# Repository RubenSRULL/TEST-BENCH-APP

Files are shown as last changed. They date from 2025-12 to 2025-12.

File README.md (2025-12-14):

# Banco de Pruebas para Motores Eléctricos con ESP32

## Descripción general

Este proyecto implementa un **banco de pruebas automatizado para motores eléctricos con hélice**, permitiendo la medición y visualización en tiempo real de **velocidad de rotación (RPM), empuje, par y consumo de corriente**.

El sistema está compuesto por:
- Un **microcontrolador ESP32** encargado del control del motor y la adquisición de sensores.
- Un **broker MQTT** para la comunicación.
- Una **aplicación web desarrollada con Dash (Python)** que actúa como interfaz de usuario (HMI).

---

## Arquitectura del sistema

Arquitectura cliente-servidor basada en MQTT:

- ESP32 → Publica datos de sensores
- Dash App → Envía comandos y visualiza resultados
- Mosquitto → Broker MQTT intermedio

---

## Características principales

- Control de velocidad del motor por PWM  
- Ensayo automático por pasos configurables  
- Medición de:
  - RPM
  - Empuje (celda de carga)
  - Par (celda de carga)
  - Corriente eléctrica
- Visualización gráfica en tiempo real  
- Interfaz web intuitiva  
- Comunicación inalámbrica vía WiFi + MQTT  
- Sistema basado en máquina de estados  

---

## Hardware utilizado

- ESP32  
- Módulo HX711 (x2)  
- Celdas de carga (x2)  
- Sensor de corriente ACS712 (30 A)
- Tacómetro  
- Controlador ESC  
- Motor brushless + hélice  
- Fuente de alimentación +12 V

---

## Software utilizado

### ESP32
- Arduino IDE
- Librerías:
  - `HX711`
  - `WiFi`
  - `ArduinoJson`
  - `PubSubClient`

### Aplicación de usuario
- Python 3.10+
- Librerías:
  - `dash`
  - `plotly`
  - `paho-mqtt`

### Comunicación
- Mosquitto MQTT Broker

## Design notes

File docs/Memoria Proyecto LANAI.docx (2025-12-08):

Máster en Informática Industrial y Robótica

Banco de pruebas para la caracterización de sistema de propulsión motor - hélice

Test bench for the characterization of the engine-propeller propulsion system

Autor

La Laguna, 8 de diciembre de 2025

Memoria Proyecto Final

Licencia

© Esta obra está bajo una licencia de Creative Commons Reconocimiento 4.0 Internacional.

Resumen

El objetivo de este trabajo ha sido el diseño y construcción de un banco de pruebas destinado a la caracterización de sistemas de propulsión motor–hélice. Para ello se integró un microcontrolador ESP32 encargado de la adquisición de datos y del control del motor BLDC, así como un sistema de comunicación MQTT que permite la transmisión de información en tiempo real hacia un dispositivo remoto.

Además, se implementó una aplicación web desarrollada en Python, mediante la cual el usuario puede supervisar el funcionamiento del sistema, enviar órdenes de control y visualizar las variables medidas durante cada ensayo.

Este banco de pruebas pretende constituir una plataforma de bajo costo, adecuada para el análisis de distintos conjuntos motor–hélice utilizados en drones.

Palabras clave: Drones, Banco de pruebas, motor BLDC, hélice, MQTT, ESP32, C, Python

Abstract

The objective of this work has been the design and construction of a test bench intended for the characterization of motor–propeller propulsion systems. For this purpose, an ESP32 microcontroller was integrated to handle data acquisition and control of the BLDC motor, as well as an MQTT communication system that enables real-time data transmission to a remote device.

In addition, a web application developed in Python was implemented, allowing the user to monitor system operation, send control commands, and visualize the variables measured during each test.

This test bench aims to provide a low-cost platform suitable for the analysis of different motor–propeller assemblies used in drones.

Keywords: Drones, Test bench, BLDC motor, Propeller, MQTT, ESP32, C, Python.

Índice general

Índice de figuras

# Capítulo 1 Introducción

## 1.1 Contexto y motivación

Los sistemas de propulsión empleados en drones han experimentado un crecimiento significativo debido a la expansión del sector de los vehículos aéreos no tripulados en ámbitos como la fotografía aérea, la agricultura de precisión, la inspección industrial y la investigación científica. Estos sistemas, formados principalmente por un motor eléctrico BLDC y una hélice, determinan el rendimiento, autonomía y capacidad de carga del dron.

Sin embargo, muchos proveedores de motores y sistemas de propulsión no ofrecen características técnicas detalladas ni datos experimentales fiables sobre su comportamiento real. En la mayoría de los casos, la información proporcionada es limitada o insuficiente para evaluar aspectos fundamentales como el empuje, la eficiencia energética o la respuesta dinámica del conjunto.

Esta falta de datos técnicos dificulta la correcta selección del sistema de propulsión, limita la capacidad de optimizar el diseño del dron y obliga a realizar pruebas adicionales. Por ello surge la necesidad de desarrollar un banco de pruebas accesible y fiable, capaz de caracterizar distintos conjuntos motor–hélice de forma objetiva.

## 1.2 Importancia de la caracterización de sistemas de propulsión

La caracterización experimental del sistema motor–hélice permite analizar:

- Empuje y par generado en función de la velocidad de giro, motor y hélices empleadas.
- Consumo eléctrico y eficiencia del sistema.
- Adecuación del conjunto a distintos perfiles de misión.

Disponer de datos medidos facilita la toma de decisiones en diseño, optimización y selección de componentes para drones.

# Capítulo 2 Marco conceptual del proyecto

En este capítulo se presentan los fundamentos necesarios para comprender el diseño y desarrollo del banco de pruebas, incluyendo antecedentes, estado del arte, objetivos y fases de ejecución. Esto permite contextualizar el trabajo dentro del campo de los drones y de los sistemas de medición.

## 2.1 Antecedentes

El continuo crecimiento del sector de los drones ha impulsado mejoras en sus sistemas de propulsión. No obstante, el acceso a bancos de pruebas profesionales suele ser costoso, y la caracterización experimental es una práctica limitada a laboratorios especializados. Con la aparición de microcontroladores avanzados y económicos como el ESP32, se abre la posibilidad de diseñar plataformas de ensayo de bajo coste para entornos académicos y de investigación.

## 2.2 Estado del arte

Actualmente existen bancos de pruebas comerciales y proyectos abiertos que permiten medir empuje, consumo y parámetros eléctricos. Muchos de ellos utilizan sensores de fuerza de alta precisión y sistemas de adquisición complejos. Paralelamente, tecnologías como MQTT se han consolidado como un estándar para la transmisión de datos en tiempo real, mientras que Python se emplea ampliamente para desarrollar interfaces de usuario intuitivas y flexibles.

## 2.3 Objetivos

Los objetivos principales son:

- Diseñar y construir un banco de pruebas de bajo coste para caracterizar sistemas de propulsión motor–hélice.
- Desarrollar un sistema que implemente IoT que permite el control remoto del banco de pruebas
- Desarrollar una aplicación web en Python que permita controlar el sistema remotamente además de adquirir y visualizar los datos.

## 2.4 Fases de desarrollo

El proyecto se estructuró en las siguientes fases:

1. Análisis de requisitos.
2. Diseño del banco de pruebas: estructura mecánica, electrónica y sensores.
3. Implementación del firmware del ESP32.
4. Desarrollo de la aplicación web en Python.
5. Pruebas, calibración y validación del sistema.
6. Documentación final y presentación de resultados.

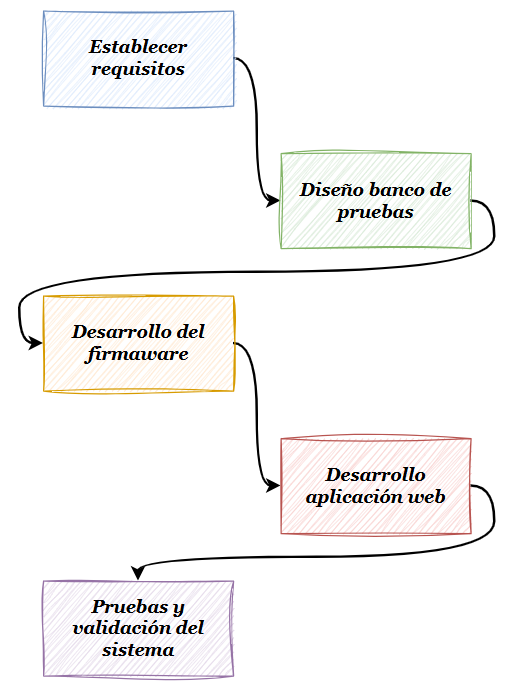
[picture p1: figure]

Ilustración 1: Fases de desarrollo del proyecto

# Capítulo 3 Desarrollo del proyecto

Una vez establecidos los antecedentes, la motivación y los objetivos del trabajo, este capítulo describe en detalle el proceso de diseño y construcción del banco de pruebas para la caracterización del sistema de propulsión motor–hélice.

## 3.1 Requisitos

Los requisitos establecidos para este proyecto son:

  - El banco de pruebas debe permitir el testeo de motores BLDC
  - El banco de pruebas también debe permitir la medición de las siguientes variables: Velocidad de giro del rotor, empuje y par generados por la hélice y la corriente consumida por el sistema
  - Debe permitir su configuración y control de forma remota a través de una aplicación web intuitiva y sencilla de controlar, permitiendo visualizar mediciones en tiempo real
  - La aplicación web creará informes con características y parámetros calculados del motor, tales como:
    - Constante de Fuerza Electromotriz K_e : relaciona la tensión entre fases con la velocidad de rotación del motor

K_e =V/(RPM)

    - Constante de Torque K_m : relaciona el par generado con la intensidad entregada al motor

K_m =T/I

    - Potencia mecánica P_(mec) de salida y potencia eléctrica P_(el) de entrada

P_(mec) =T⋅ω P_(el) =V⋅I

    - Rendimiento η : mide la eficiencia en la conversión de energía eléctrica en energía mecánica del rotor

η=(P_(mec))/(P_(el))

## 3.2 Diseño mecánico del banco de pruebas

El banco de pruebas se diseñó para medir de forma controlada el empuje y el par reactivo generados por el motor eléctrico con hélice por medio de dos celdas de carga. La disposición de estas celdas de carga se muestra en la figura X:

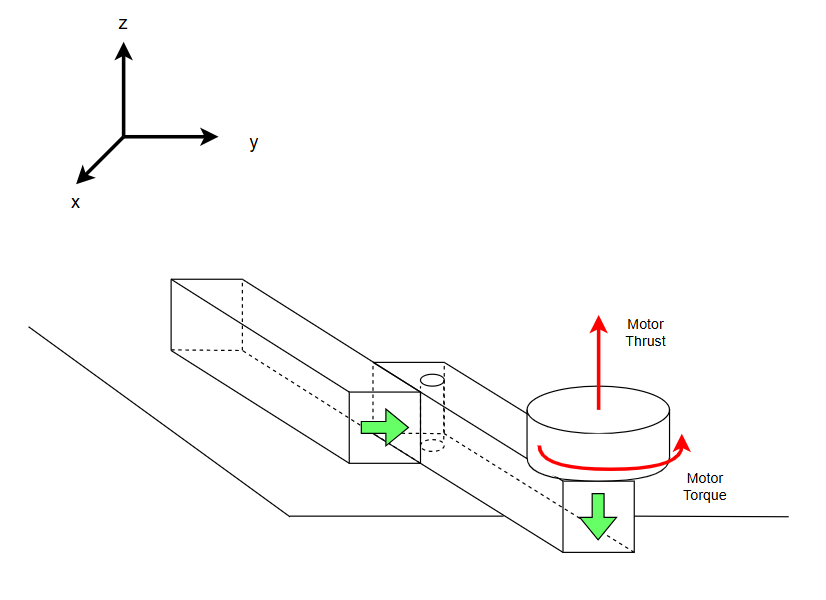
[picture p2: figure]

Ilustración 2: Diagrama que muestra la colocación de las celdas de carga y fuerzas que genera el rotor

La estructura principal está formada por dos celdas de carga, cada una configurada para trabajar en un único eje gracias a la presencia de orificios mecanizados en su sección central (ver figura X). Estos vaciados reducen la rigidez estructural en una sola dirección, forzando a la celda a deformarse únicamente en el eje previsto y evitando que absorba esfuerzos en otros planos.

Ilustración 3: Diagrama que muestra las deformaciones admitidas por la celda de carga gracias a su diseño

De este modo, cada celda cumple una función específica dentro del sistema: Una de ellas se encarga de registrar la componente horizontal asociada a la reacción del par motor, mientras que la otra mide la componente vertical correspondiente al empuje. Las figuras X y X muestras los diagramas de cuerpo libre (DCL) de ambas celdas de carga:

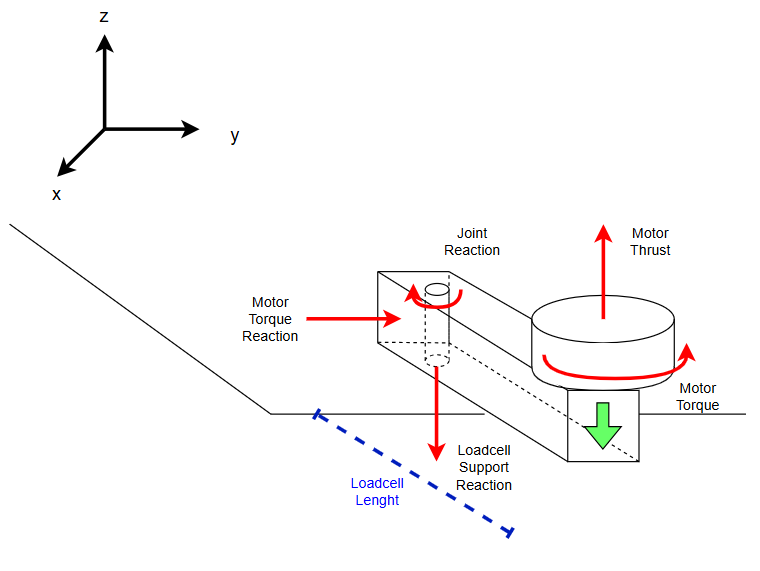
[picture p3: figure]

Ilustración 4: Diagrama de cuerpo libre (DCL) de la celda de carga 1, encargada de medir el empuje

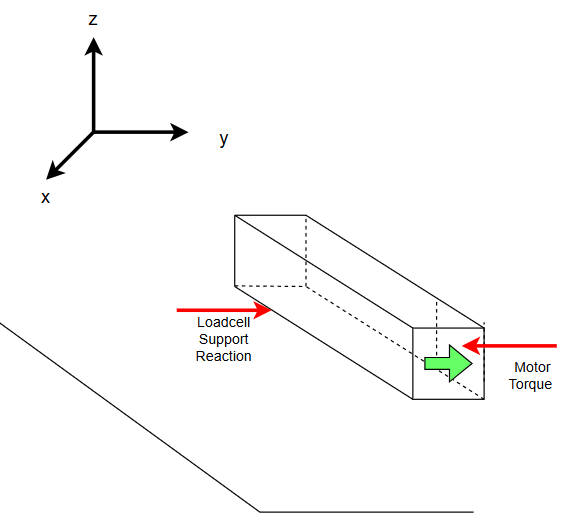
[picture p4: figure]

Ilustración 5: Diagrama de cuerpo libre (DCL) de la celda de carga 2, encargada de medir el par

## 3.3 Desarrollo del sistema electrónico

El sistema electrónico del banco de pruebas se diseñó con el objetivo de capturar en tiempo real las magnitudes físicas generadas por el motor brushless —empuje, par reactivo, corriente y velocidad de giro— y controlar su régimen de funcionamiento mediante un variador electrónico de velocidad (ESC). La Figura X muestra el esquema general de interconexión del hardware implementado sobre protoboard durante la fase de desarrollo.

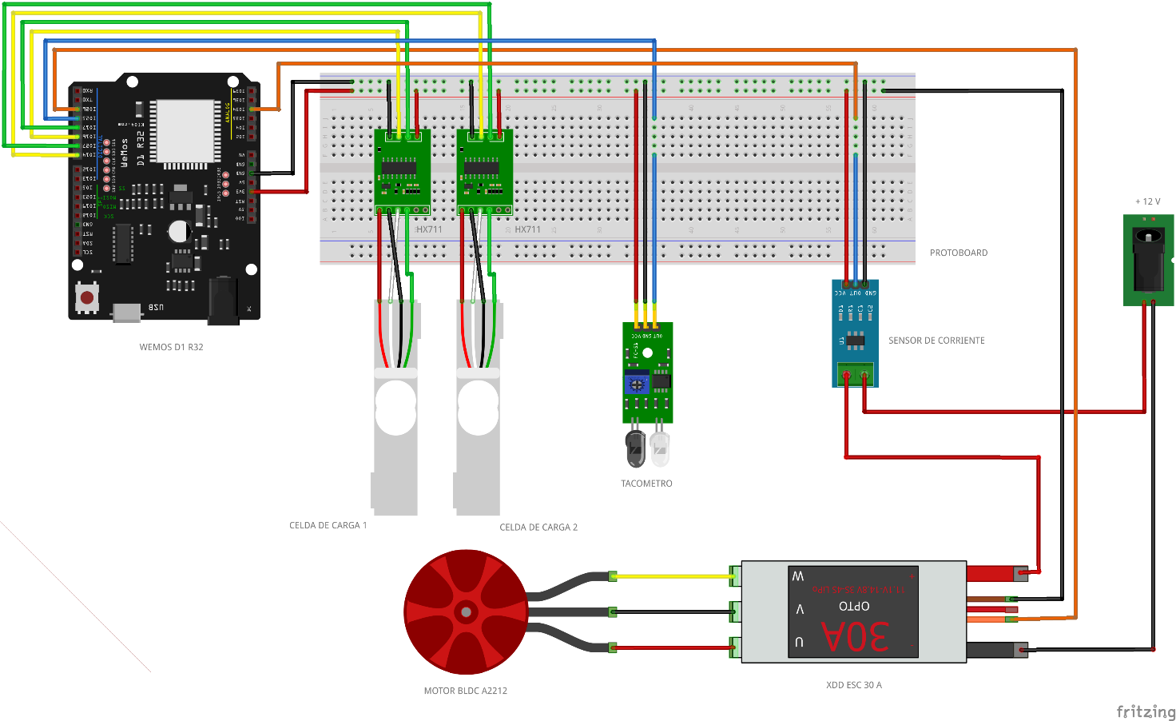
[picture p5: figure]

Ilustración 6: diagrama del circuito eéctrico que muestra la conexión de los componentes que conforman el banco de pruebas

### 3.3.1. Unidad de control: ESP32 (WEMOS)

Como núcleo del sistema se empleó un ESP32 Wemos D1 R32, una placa que combina la filosofía de Arduino UNO con la potencia del microcontrolador ESP32. Esta elección permitió disponer de:

- Conectividad WiFi integrada, necesaria para la comunicación vía MQTT.
- Gran número de entradas y salidas digitales.
- Entradas analógicas de 12 bits para la lectura del sensor de corriente.
- Temporizadores y PWM de alta resolución para control preciso del ESC.

El microcontrolador gestiona la lectura de todos los sensores y ejecuta el control del motor, además de enviar la información telemétrica y recibir los parámetros del ensayo a través de comunicación MQTT.

### 3.3.2. Medición del empuje y par

Para la medición de las fuerzas generadas por el motor se utilizaron dos celdas de carga tipo barra, cada una conectada a un módulo amplificador HX711. Estos convertidores analógico-digitales de 24 bits permiten obtener mediciones de muy baja señal eléctrica con excelente resolución.

Las 2 celdas se conectaron de la siguiente manera:

- HX711 de celda 1 (empuje)
  - DOUT (señal de datos) → pin IO16
  - SCK (señal de reloj) → pin IO17
- HX711 de celda 2 (par)
  - DOUT (señal de datos) → pin IO26
  - SCK (señal de reloj) → pin IO27

Los módulos se alimentan desde la protoboard, con una línea común de 3.3 V y GND. La señal amplificada se lee directamente desde el ESP32, desde donde se procesa y se filtra para garantizar estabilidad en las mediciones.

### 3.3.3. Medición de la velocidad del motor (tacómetro)

La lectura de las revoluciones por minuto se realizó mediante un módulo tacómetro basado en un sensor óptico reflexivo. Este dispositivo detecta el paso de una superficie reflectante adherida al rotor del motor y envía pulsos al microcontrolador.

Este sensor se conectó de la siguiente manera:

  - Salida de pulsos digital → pin IO25
  - Alimentación → 3.3 V y GND desde la protoboard

El firmware se encarga de medir la frecuencia de los pulsos y convertirla en RPM, permitiendo sincronizar las mediciones con el funcionamiento real del motor.

### 3.3.4. Sensor de corriente

El consumo del motor se midió mediante un sensor de corriente tipo ACS712/ACS758, conectado en serie con la línea positiva de alimentación del ESC. Este módulo proporciona una señal analógica proporcional a la corriente instantánea, la cual se conectó al pin analógico IO34 del ESP32.

Dado que la salida del sensor es analógica, se emplea una lectura ADC y un proceso de calibración para convertir los valores en amperios.

### 3.3.5. Control del motor mediante ESC

El motor brushless A2212 se controla mediante un ESC de 30 A, el cual se alimenta desde una fuente independiente de 12 V. La señal de control PWM se generó desde el pin IO14 del ESP32.

El ESC recibe la señal, regula la potencia entregada a las bobinas del motor y permite un control continuo del régimen de giro.

### 3.3.6. Alimentación

El sistema dispone de dos niveles de tensión principales:

- 12 V → Para el ESC y el motor.
- 5 V → Para los sensores y el ESP32 (a través del regulador integrado de la protoboard o de la entrada VIN del Wemos D1 R32).

Todas las conexiones comparten una referencia común de GND, indispensable para evitar ruido eléctrico y garantizar lecturas estables.

## 3.4 Desarrollo del firmware ESP32 (C++)

El firmware ha sido desarrollado en C++ en el IDE Arduino. El programa funciona como una máquina de estados, cuyo estado cambia en función de la acción recibida por MQTT.

### 3.4.1 setup()

Función encargada de la configuración inicial del sistema. Se encarga de:

- Inicializar comunicación serie
- Configurar WiFi, MQTT y sensores
- Configurar interrupciones y PWM
- Dejar listo el sistema para recibir comandos y transicionar de estado

Ilustración 7: Algoritmo de setup()

### 3.4.2 loop()

Bucle principal del sistema basado en una máquina de estados. Se encarga de:

- Mantener la conexión MQTT activa
- Ejecutar acciones según el estado actual:
  - STOP: sistema detenido
  - TESTING: ensayo en ejecución
  - TARE: tarado de balanzas
  - CALIB: calibración de balanzas
- Gestionar transiciones entre estados

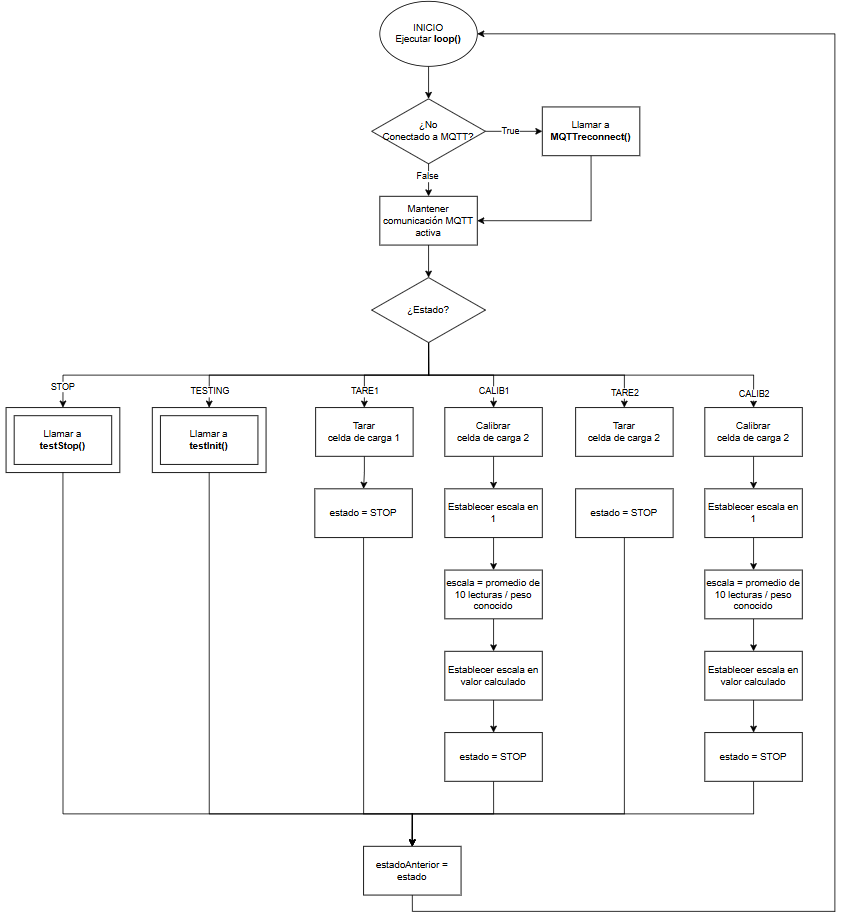
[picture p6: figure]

Ilustración 8: Algoritmo de loop()

### 3.4.3 Funciones llamadas desde el setup()

- configWifi(): configura la conexión del ESP32 a una red WiFi. Se encarga de:
  - Inicializar el módulo WiFi en modo estación
  - Conectarse a la red especificada
  - Esperar hasta confirmar conexión exitosa
- configMQTT(): inicializar la configuración del cliente MQTT. Se encarga de:
  - Definir el bróker MQTT y el puerto
  - Ajustar el tamaño del buffer
  - Registrar la función de callback para recepción de mensajes
- configHX711(): inicializa y verifica las celdas de carga. Se encarga de:
  - Configurar los pines de datos y de reloj en ambos módulos HX711
  - Esperar a que los módulos HX711 estén listos
  - Confirmar la disponibilidad de las balanzas
- testStop(): detiene completamente el ensayo Se encarga de:
  - Detener el motor (PWM = 0)
  - Reiniciar todas las variables de medición

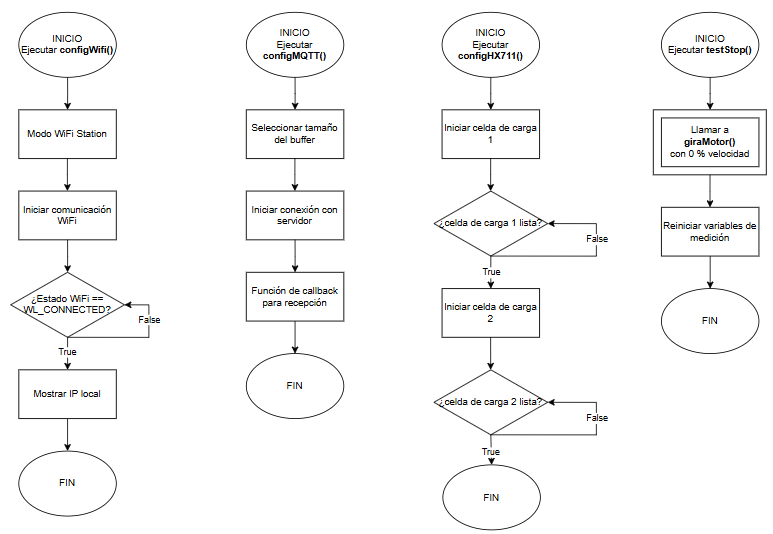
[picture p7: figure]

Ilustración 9: Algoritmos de configWifi(), configMQTT(), configHX711(), testStop()

### 3.4.4 Función testInit()

Esta función gestiona la secuencia del ensayo automático del rotor. Se encarga de:

- Incrementar la velocidad del motor por pasos.
- Respetar el tiempo configurado entre incrementos.
- Medir RPM, empuje, par y consumo según configuración.
- Publicar los datos obtenidos vía MQTT.
- Controlar ciclos repetitivos del ensayo.
- Finalizar el test cuando se alcanzan las condiciones límite.

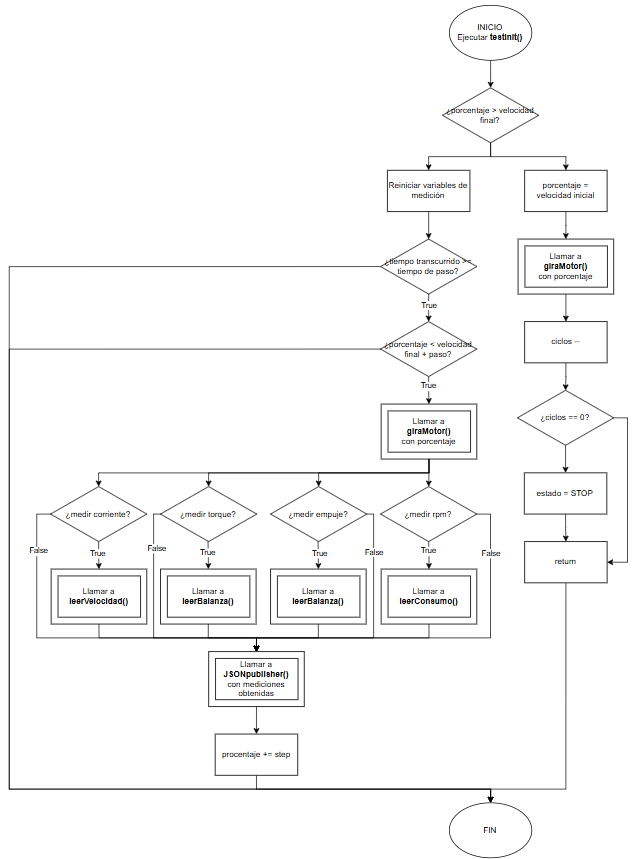
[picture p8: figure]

Ilustración 10: Algoritmo de testInit()

### 3.4.5 Función JSONpublisher()

Publica los datos del ensayo en formato JSON por MQTT: Se encarga de:

- Construir un mensaje JSON con las variables medidas
- Enviar los datos al tópico de salida MQTT

Ilustración 11: Algoritmo de JSONpublisher()

### 3.4.6 Otras funciones llamadas desde el loop()

- leerVelocidad(): Calcula la velocidad de rotación del motor en RPM a partir del intervalo medido por la interrupción. Se encarga de:
  - Leer de forma segura el intervalo entre pulsos
  - Convertir el periodo de pulso a revoluciones por segundo
  - Transformar el valor a revoluciones por minuto (RPM)
- giraMotor(int pct): controla la velocidad del motor mediante señal PWM. Se encarga de:
  - Convertir un porcentaje de velocidad (0 – 100 %) a un ciclo de trabajo PWM
  - Aplicar el valor al pin de control del motor mediante ledcWrite()

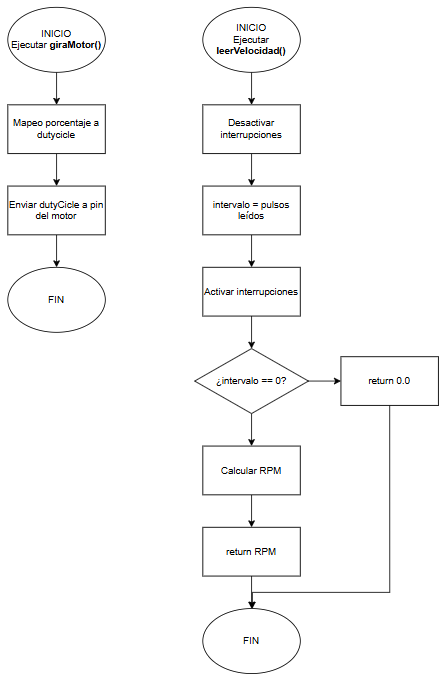
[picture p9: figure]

Ilustración 12: Algoritmos de giraMotor() y leerVelocidad()

- leerBalanza(): Obtiene el valor de una celda de carga conectada mediante el módulo HX711. Se encarga de:
  - Leer múltiples muestras del HX711
  - Retornar el peso promedio en unidades calibradas
- leerConsumo(): lee el consumo de corriente del sistema a través de un sensor analógico. Se encarga de:
  - Promediar múltiples lecturas analógicas para reducir ruido
  - Convertir la lectura ADC a voltaje
  - Calcular la corriente usando la constante del sensor

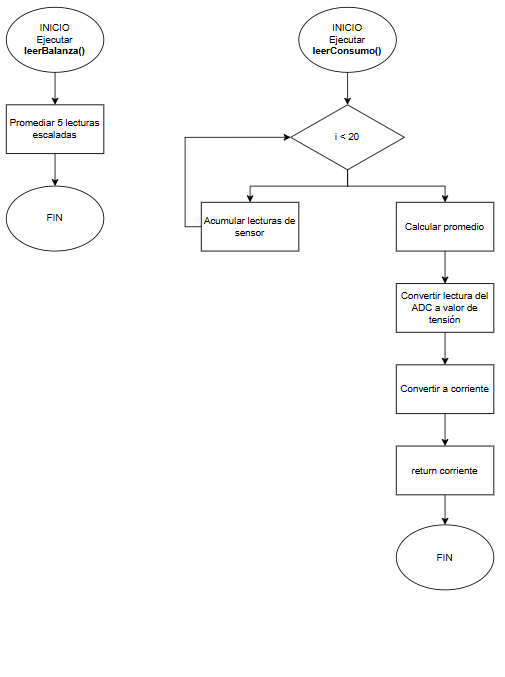
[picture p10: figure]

Ilustración 13: Algoritmos de leerBalanza() y leerConsumo()

### 3.4.7 Función de callback MQTT

Esta función se ejecuta al recibir un mensaje MQTT. Se encarga de:

- Decodificar mensajes JSON recibidos
- Interpretar comandos (start, stop, tare, calibrate)
- Actualizar parámetros internos del sistema para realizar el ensayo
- Cambiar el estado del sistema según la orden recibida

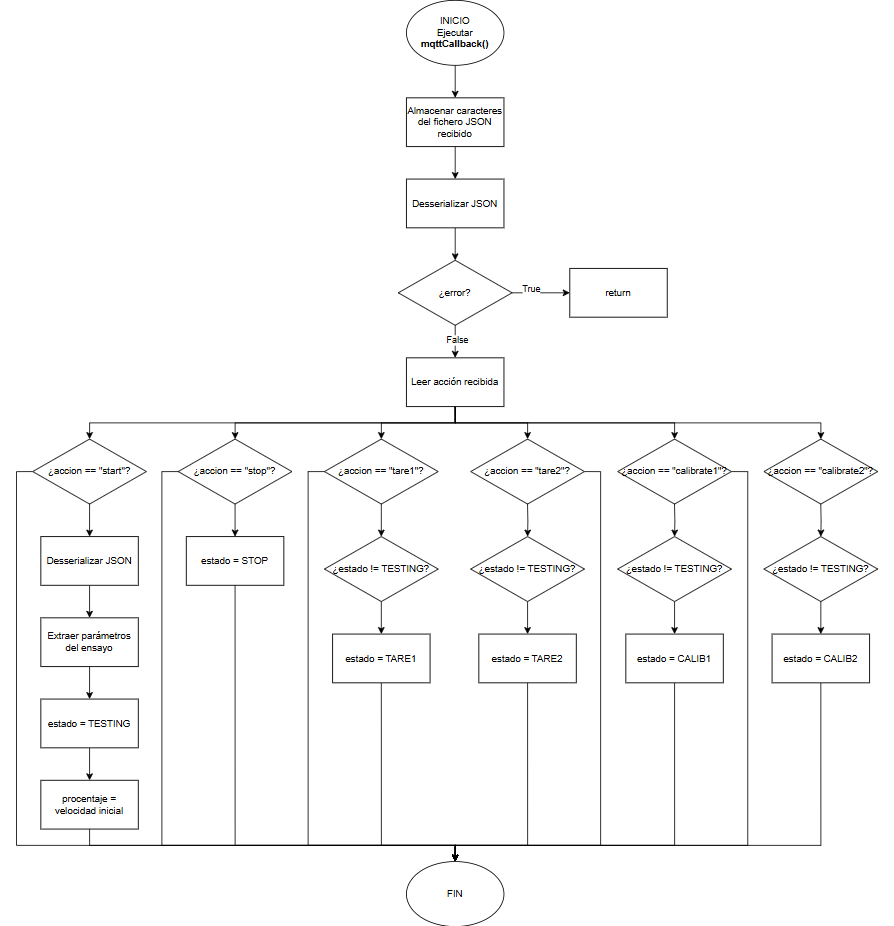
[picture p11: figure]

Ilustración 14: Algoritmo de callback de recepción MQTT, mqttCallback()

### 3.4.8 Función de interrupción para leer velocidades

Función de interrupción asociada al tacómetro. Se ejecuta cada vez que se detecta un pulso (flanco descendente) proveniente del sensor de velocidad.

Se encarga de:

- Medir el tiempo entre pulsos consecutivos en microsegundos
- Filtrar rebotes ignorando pulsos demasiado cercanos
- Guardar el intervalo de tiempo para el cálculo de RPM

Ilustración 15: Función de interrupción pulseISR()

## 3.5 Desarrollo de la aplicación web (Python)

Para el desarrollo de la aplicación de creó una librería para gestionar la comunicación MQTT, el cálculo de parámetros del motor y generar las figuras y gráficas oportunas

### 3.5.1. Script banco de pruebas: testBenchApp.py

- Inicio: ver métodos con mayor detalle en sección 3.5.2
  - Instanciar objeto de la clase TestBench()
  - Llamar al método configMQTTBroker(), indicando:
    - IP del boker
    - Puerto del bróker
    - Carpeta principal de Mosquitto
    - Archivo .conf de Mosquitto
  - Llamar al método configMQTT() indicandi:
    - Tópico de envío
    - Tópico de recepción
- Función principal → main(): Se encarga de lanzar servidor web Dash

Ilustración 16: Función main()

- Interfaz gráfica: Define la estructura visual completa de la aplicación web a partir de HTML y CSS básico. Se encarga de:
  - Organizar la información en secciones:
    - Parámetros de la hélice
    - Parámetros del motor
    - Configuración del ensayo
    - Control de celdas de carga
    - Control de inicio / parada
    - Visualización gráfica
  - Proporcionar campos de entrada, botones y gráficos interactivos
  - Servir como interfaz hombre – máquina (HMI) del banco de pruebas

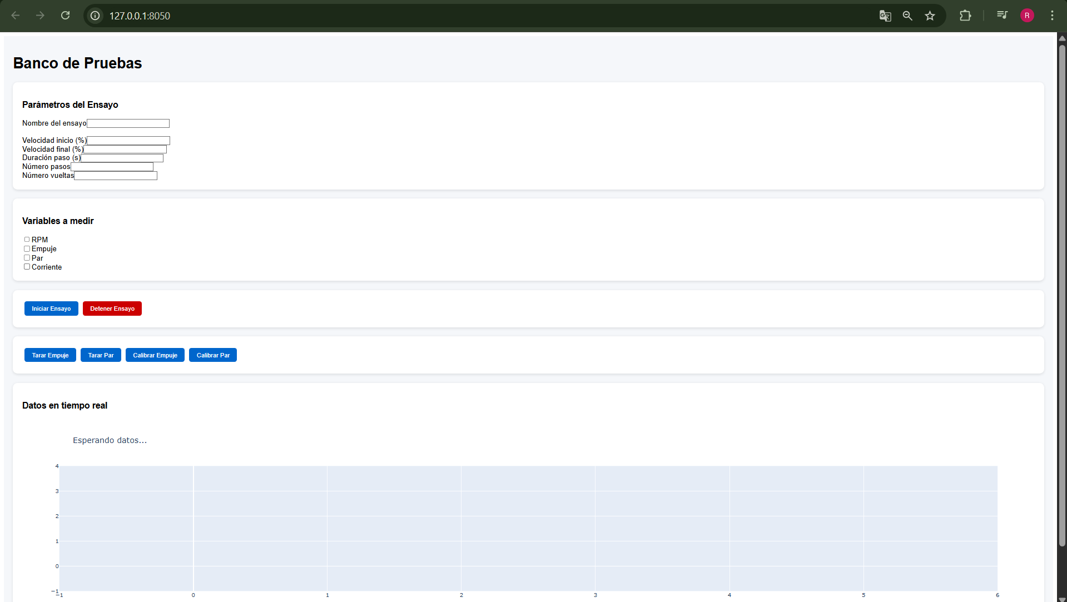
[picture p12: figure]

Ilustración 17: Interfaz de la aplicación web para control y configuración del banco de pruebas

- Callbacks de control del ensayo
  - startTest(): callback asociado al botón de “iniciar ensayo”. Se encarga de:
    - Leer los valores introducidos por el usuario en la interfaz
    - Construir un mensaje JSON con:
      - Parámetros del ensayo
      - Configuración de velocidad
      - Variables a medir
    - Enviar el comando “start” al ESP32 mediante MQTT
    - Iniciar el proceso de ensayo remoto
  - stopTest(): callback asociado al botón “detener ensayo”. Se encarga de:
    - Enviar un mensaje MQTT con la acción “stop”
    - Ordenar al ESP32 detener el motor y finalizar el ensayo
    - Garantizar una parada segura del sistema

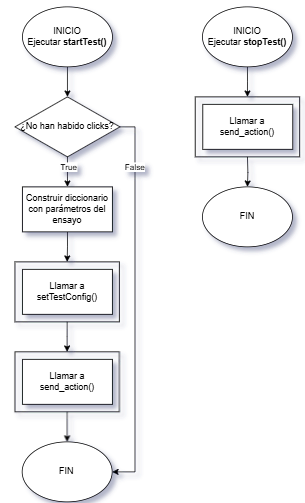
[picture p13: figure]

Ilustración 18: Callbacks asociados a elementos HTML: startTest(), stopTest ()

  - tare1(), tare2(): ordena el tarada de las celdas de carga de empuje y de par respectivamente. Se encargan de:
    - Enviar el comando “tare1” o “tare2” por MQTT
  - calibrate1(), calibrate2(): ordena la calibración de las celdas de empuje. Se encargan de:
    - Enviar el comando “calibrate1” o “calibrate2” por MQTT
  - update_graph(): actualiza el gráfico en tiempo real de las variables medidas durante el ensayo. Se encarga de:
    - Representar empuje, par y corriente en función de la velocidad
    - Actualizar el gráfico a intervalos regulares definidos por el temporizador

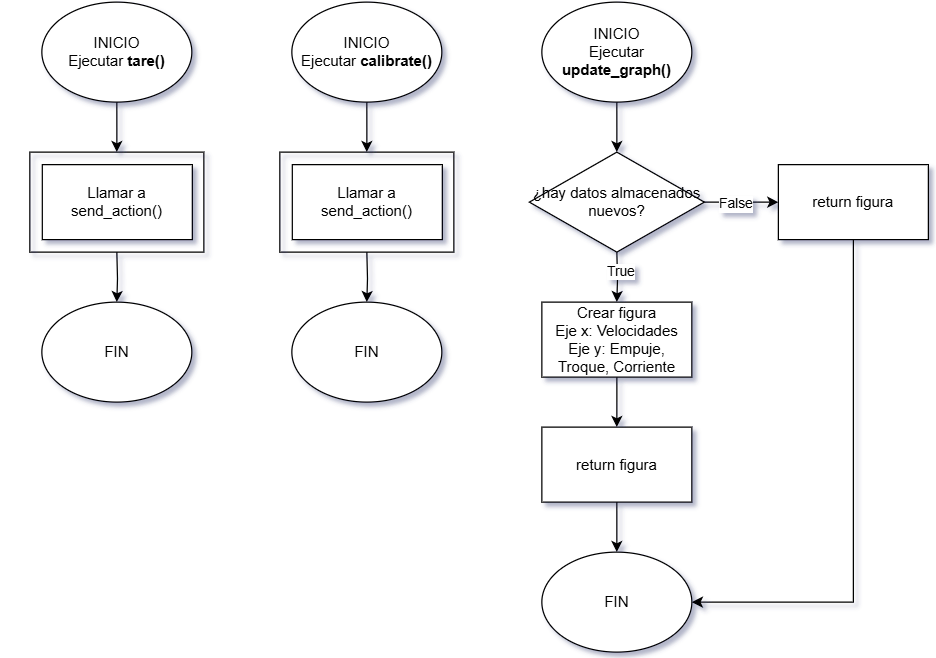
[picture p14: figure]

Ilustración 19: Callbacks asociados a elementos HTML: tare(), calibrate(), update_graph()

- Función para envío MQTT: se encarga de enviar las acciones en formato .json. Si además de la acción, hay que enviar datos, los añade al diccionario que conforma el .json

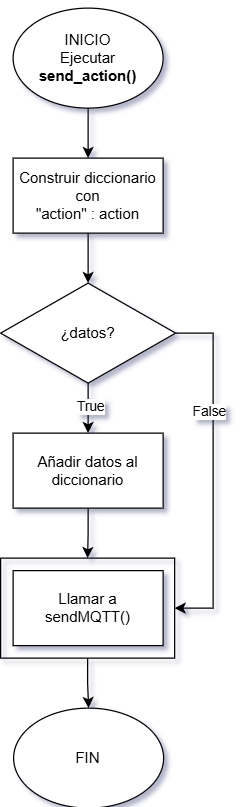
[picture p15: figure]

Ilustración 20: función para enviar datos

### 3.5.2. Librería TestBench.py: Clase TestBench()

- Constructor __init__(): se encarga de instanciar un objeto de la clase TestBench. Además, se encarga de:
  - Inicializar los atributos
  - Almacenar las rutas para almacenar las figuras e informes generados
- Configurar Broker MQTT → configMQTTBroker(): Inicializa el bróker Mosquitto MQTT en segundo plano si no se encuentra ya en ejecución. Se encarga de:
  - Verificar si Mosquitto está activo en el sistema
  - Lanzar el bróker de manera automática si no está corriendo
  - Garantizar la disponibilidad del servidor MQTT antes de iniciar la aplicación

Ilustración 21: Algoritmo configMQTTBroker ()

- Configurar comunicación MQTT → configMQTT(): Inicializa el cliente MQTT y establece la comunicación con el bróker. Se encarga de:
  - Crear el cliente MQTT con protocolo MQTTv5
  - Definir la función de callback para mensajes entrantes
  - Conectarse al bróker MQTT
  - Suscribirse al tópico de recepción de datos
  - Mantener el bucle MQTT activo en segundo plano

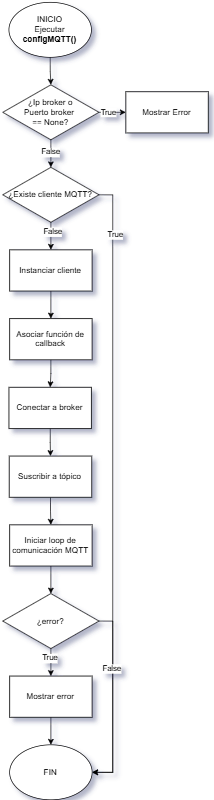
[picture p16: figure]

Ilustración 22: Algoritmo configurarMQTT()

- Enviar mensaje MQTT → sendMQTT(): Función empleada para publicar datos vía MQTT a cierto tópico. Se encarga de:
  - Comprobar si se configuró la comunicación MQTT
  - Publicar datos al tópico indicado

Ilustración 23: Enviar datos por MQTT

- Recibir mensaje MQTT → receiveMQTT(): Función de callback que se ejecuta cada vez que se recibe un mensaje MQTT desde el ESP32. Se encarga de:
  - Decodificar el mensaje JSON recibido
  - Extraer las variables de ensayo (velocidad, empuje, par y corriente)
  - Almacenar los valores en listas de datos para visualización
  - Mostrar por consola los datos recibidos para depuración

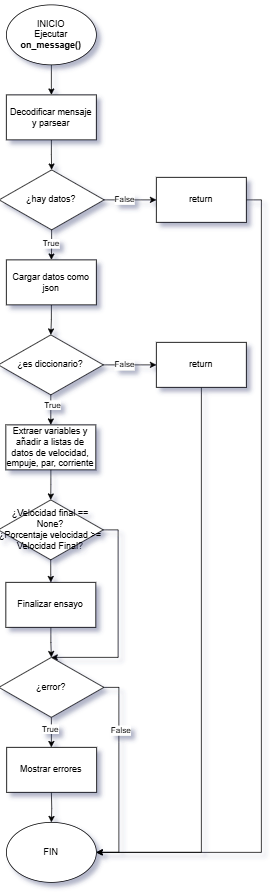
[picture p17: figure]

Ilustración 24: Callback para gestión de mensajes MQTT

- Finalizar ensayo → finish(): Se encarga de llamar a los métodos encargados de generar el informe, las figuras y de desconectar la comunicación MQTT

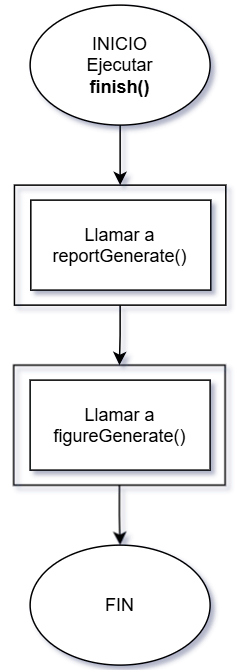
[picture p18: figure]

Ilustración 25: Método para finalizar ensayo

- Desconectar MQTT → disconnect(): Este método evita que la comunicación MQTT y el puerto queden permanentemente activos escuchando, cerrando la conexión

Ilustración 26: Método para desconectar MQTT

- Calcular parámetros rotor → computeParameters(): Este método realizar el cálculo de los parámetros más destacados del rotor

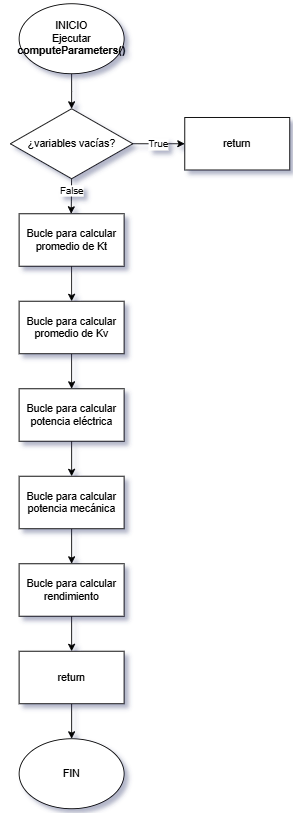
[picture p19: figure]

Ilustración 27: Algoritmo para calcular parámetros del rotor

- Generar informe → reportGenerate(): Este método genera un fichero .csv a partir de los datos calculados

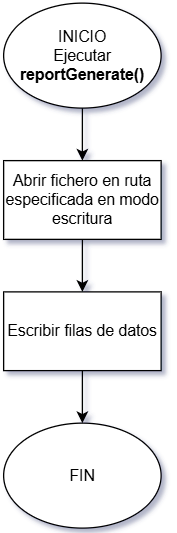
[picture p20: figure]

Ilustración 28: Método para generar informe con los resultados del ensayo

- Generar figuras → figureGenerate(): Este método genera las gráficas que caracterizan el comportamiento del motor

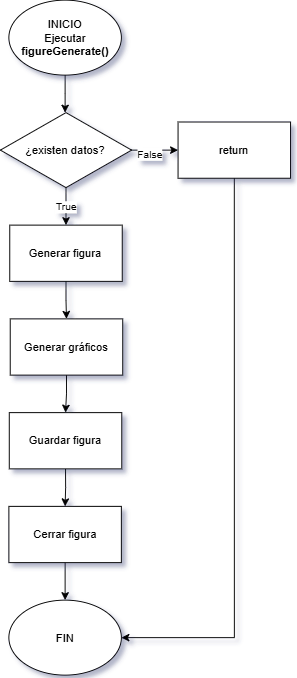
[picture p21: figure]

Ilustración 29: Algoritmo para generar gráficos con datos en tiempo real

- Añadir parámetros de ensayo → setTestConfig(): Este método asigna las variables del ensayo a los respectivos atributos

## 3.6 Implementación sistema de comunicación MQTT

Para garantizar una comunicación bidireccional, robusta y en tiempo real entre el firmware del ESP32 y la aplicación web desarrollada en Python, se implementó un sistema basado en el protocolo MQTT (Message Queuing Telemetry Transport). Este protocolo, ampliamente utilizado en aplicaciones IoT, destaca por su bajo consumo de ancho de banda y su simplicidad.

El esquema general de funcionamiento se ilustra en la Figura X, donde se observa la interacción entre los diferentes elementos del sistema: el ESP32, el broker Mosquitto, y el script Python ejecutado en el PC.

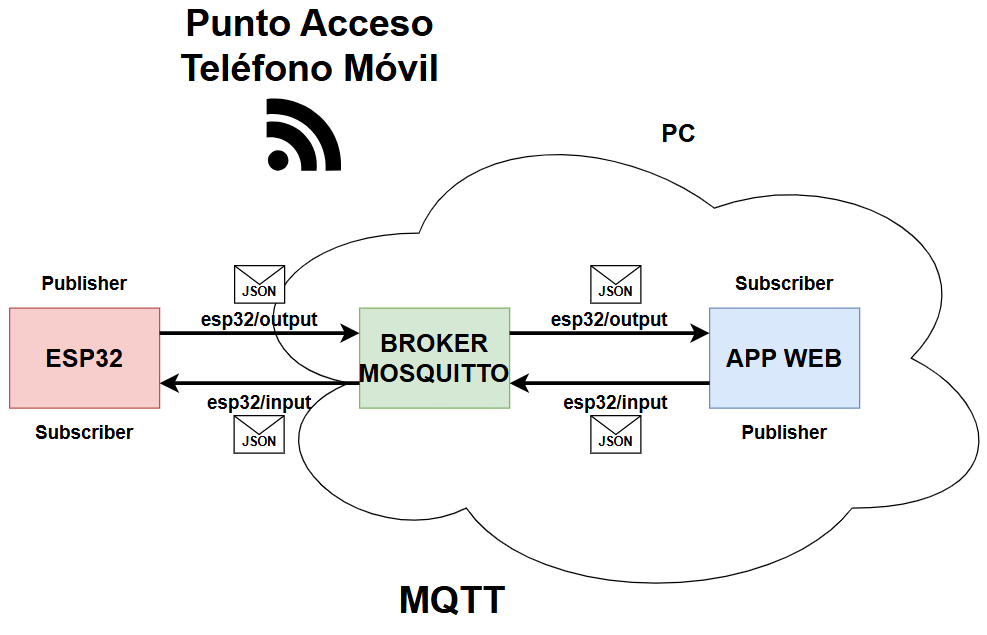
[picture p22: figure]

Ilustración 30: Esquema de comunicación MQTT implementado

El broker MQTT, instalado en el ordenador mediante el servicio Mosquitto, actúa como intermediario encargado de recibir, almacenar y distribuir los mensajes publicados por los dispositivos suscritos a los diferentes tópicos. Para este proyecto se definieron dos canales principales:

- esp32/output: utilizado por el ESP32 para publicar datos de telemetría, incluyendo las lecturas de las celdas de carga, el estado del motor y cualquier otra variable relevante del sistema.
- esp32/input: canal empleado por la aplicación Python para enviar comandos de control al microcontrolador, tales como el ajuste de la señal PWM, cambios en los parámetros de medición o la solicitud de acciones específicas.

El ESP32, por tanto, se comporta simultáneamente como publicador y suscriptor, permitiendo tanto el envío de información sensorial como la recepción de instrucciones por parte del software de control. La aplicación Python replica esta doble funcionalidad, actuando como suscriptor para obtener en tiempo real los datos de operación, y como publicador para transmitir comandos al microcontrolador.

Todos los mensajes se estructuran en formato JSON, lo que facilita su interpretación en ambos extremos y permite una comunicación ordenada y extensible.

# Capítulo 4 Conclusiones y líneas futuras

## 4.1 Conclusiones

A lo largo del proyecto se ha logrado diseñar y construir un banco de pruebas funcional para la caracterización de sistemas de propulsión motor–hélice empleados en drones. El sistema desarrollado, basado en un microcontrolador ESP32, permite adquirir datos como empuje, par, corriente y velocidad del motor— de forma fiable y en tiempo real. La integración del protocolo MQTT ha demostrado ser una solución eficaz para la transmisión remota de información, posibilitando el control del banco desde una aplicación web desarrollada en Python.

## 4.2 Líneas de trabajo futuro

Aunque el banco de pruebas desarrollado es plenamente operativo, existen múltiples posibilidades de mejora y ampliación. Entre las líneas de trabajo más relevantes se proponen las siguientes:

- Mejoras en la precisión de los sensores: Incorporar sensores de fuerza de mayor resolución o sistemas de medición de par permitiría obtener una caracterización más completa del motor y la hélice.
- Mejoras mecánicas y de seguridad: Añadir protecciones adicionales, soportes ajustables que permitan colocar motores de otros tamaños y configuración, así como sistemas antivibración para mejorar la fiabilidad del banco.
- Integración con bases de datos externas: Crear un repositorio de caracterizaciones que pueda compartirse entre usuarios, facilitando la comparación de diferentes motores y hélices.

# Capítulo 5 Summary and Conclusions

## 5.1 Conclusions

This project developed a low-cost test bench for characterizing drone motor–propeller systems. The platform includes a mechanical structure, an ESP32-based electronic system, MQTT communication and a Python web application. It measures thrust, torque, electrical consumption and motor speed in real time, enabling objective evaluation of propulsion performance.

The system meets the proposed objectives, providing reliable measurements and a flexible architecture suitable for academic and research use.

## 5.2 Future work

Possible improvements include higher-precision sensors, mechanical enhancements for stability and safety, and integration with external databases to share and compare propulsion data.

# Capítulo 6 Códigos y algoritmos

## 6.1 Códigos Aplicación Web y Firmware del Banco de Pruebas

Los códigos y estructura de ficheros del proyecto pueden encontrarse en el siguiente repositorio:

https://github.com/RubenSRULL/TEST-BENCH-APP.git

# Capítulo 7 Características electrónicas

## 7.1 Microcontrolador WEMOS D1 R32

El núcleo del sistema es el WEMOS D1 R32, una placa que integra el microcontrolador ESP32. Este dispositivo ofrece un equilibrio adecuado entre potencia de procesamiento, facilidad de programación y conectividad inalámbrica.

Sus principales ventajas y características de interés para el banco de pruebas son:

- Microprocesador de doble núcleo a 240 MHz, capaz de ejecutar de forma paralela tareas de control del motor, adquisición de datos y comunicación. En este proyecto no se hace uso del segundo núcleo, pero la velocidad de procesamiento es imprescindible para garantizar un tiempo real.
- Wi-Fi integrado, lo que permite establecer comunicaciones remotas sin hardware adicional, permitiendo la programación de dispositivos IoT.
- Amplia disponibilidad de periféricos, tales como ADC, PWM, I2C y UART, necesarios para gestionar sensores, amplificadores y controladores.
- Compatibilidad con Arduino y ESP-IDF, lo que facilita el desarrollo del firmware en plataformas como Arduino – IDE.

El microcontrolador se encarga de leer los sensores, aplicar filtrado y conversión de datos, controlar el variador del motor BLDC y publicar los valores a través de MQTT para su visualización en la aplicación web.

Ilustración 31: Pinout ESP32 (Wemos D1 R32)

https://doc.riot-os.org/group__boards__esp32__wemos__d1__r32.html

## 7.2 Sensores

### 7.2.1 Sensor de empuje

El empuje generado por la hélice se mide mediante una celda de carga dimensionada para soportar las fuerzas máximas esperadas. La celda se conecta al amplificador HX711, un convertidor analógico-digital de 24 bits diseñado específicamente para aplicaciones de pesaje.

El HX711 permite obtener mediciones estables y de alta resolución, incluso con variaciones pequeñas de fuerza.

El sistema realiza un calibrado y tarado previo que convierte las lecturas en valores de empuje expresados en gramos.

### 7.2.2 Sensor de par

Para medir el par transmitido por el motor se emplea una segunda celda de carga acoplada mecánicamente de manera que registre el esfuerzo torsional.

También se utiliza un HX711 independiente para amplificar y digitalizar la señal.

Para calcular el par se lee el valor devuelto por el HX711 y se multiplica por el brazo de palanca (longitud de la celda de carga)

M_(rotor) =F_(leida) ⋅L

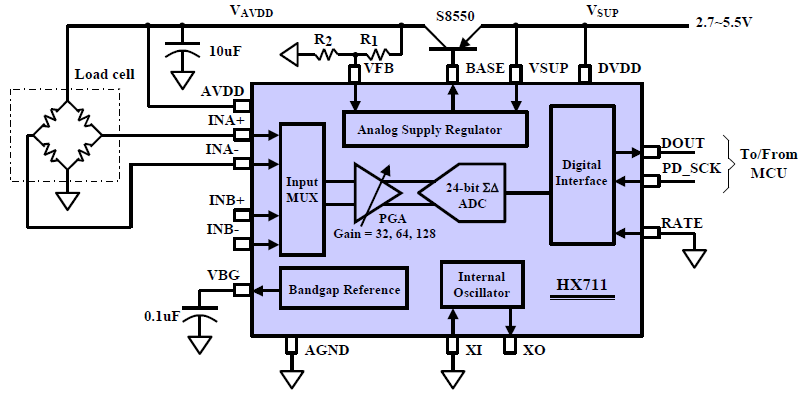
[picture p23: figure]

Ilustración 32: Diagrama de bloques del módulo amplificador HX711

https://www.alldatasheet.com/datasheet-pdf/pdf/1132222/AVIA/HX711.html

### 7.2.3 Sensor de velocidad de rotación

La velocidad de giro se mide mediante un sensor infrarrojo que detecta el paso periódico de una cinta negra colocada en el rotor del motor. Este método es ventajoso porque:

- No añade carga mecánica al eje del motor.
- Mantiene una alta velocidad de respuesta.
- Es resistente a interferencias electromagnéticas generadas por el motor.

El ESP32 cuenta el tiempo transcurrido entre 2 interrupciones consecutivas (generadas cada vez que la cinta pasa por delante del sensor), siendo posible estimar el tiempo que tarda en realizar una revolución y estimando de esta manera la velocidad:

Ω=(1 rev)/(Δt)

Ilustración 33: Diagrama eléctrico del módulo / sensor empleado para medir la velocidad de rotación (tacómetro)

https://muman.ch/muman/muman-infrared-reflective-sensor.htm

### 7.2.4 Sensor de corriente

El consumo eléctrico del motor se monitoriza mediante el módulo ACS517, basado en el chip ACS712ELC-05B.

Este sensor utiliza el efecto Hall para medir la corriente de forma aislada, evitando interferencias y mejorando la seguridad del circuito.

El ACS712 permite detectar corrientes positivas y negativas, con buena linealidad y un tiempo de respuesta adecuado para registrar cambios rápidos en el consumo del motor durante las variaciones de carga y velocidad.

El ESP32 habilita un pin conectado al ADC interno para realizar lecturas analógicas de este sensor, convirtiendo el valor de tensión entregado en un valor de corriente mediante un factor de conversión

I_(estimada) =(V_(leido) -V_(0(offset)) )⋅C_(cal factor)

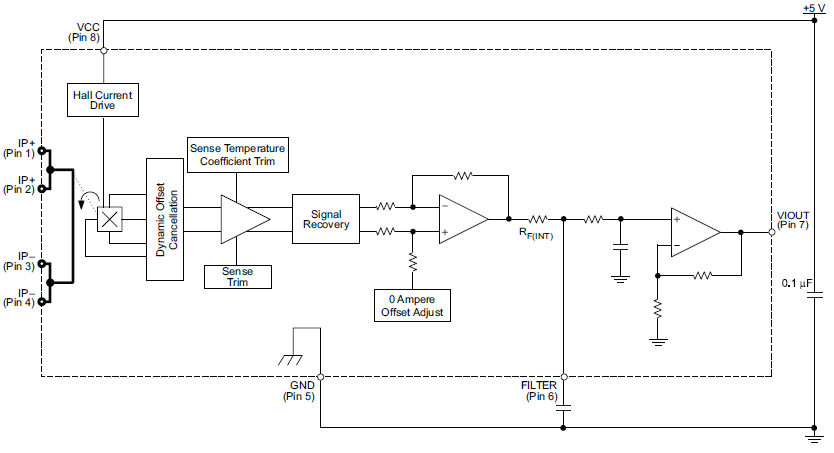
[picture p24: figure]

Ilustración 34: Diagrama de bloques / eléctrico del sensor de corriente

https://www.alldatasheet.com/datasheet-pdf/pdf/168327/ALLEGRO/ACS712ELCTR-05B-T.html

Bibliografía

[1] Plotly Dash. Dash Documentation & User Guide. Disponible en: https://dash.plotly.com/

[2] Eclipse Paho. paho-mqtt (versión 2.1.0). Disponible en: https://pypi.org/project/paho-mqtt/

[3] Python Software Foundation. json — JSON encoder and decoder — documentación de Python 3. Disponible en: https://docs.python.org/es/3/library/json.html

[4] bogde. HX711: Arduino library to interface the Avia Semiconductor HX711 24-Bit ADC. Disponible en: https://github.com/bogde/HX711

[5] knolleary. PubSubClient: Arduino client library for MQTT. Disponible en: https://github.com/knolleary/pubsubclient

[6] bblanchon. ArduinoJson: JSON library for Arduino and embedded C++. Disponible en: https://github.com/bblanchon/ArduinoJson

[7] Electrónica El Faro. Módulo del sensor de corriente. Disponible en: https://electronicaelfaro.com/modulo-del-sensor-de-corriente

[8] Electrónica El Faro. Celda de carga 5 kg (5–10 V). Disponible en: https://electronicaelfaro.com/celda-de-carga-5kg-5-10v-celula

[9] Electrónica El Faro. Sensor de presión de alta precisión HX711 (24 bits). Disponible en: https://electronicaelfaro.com/sensor-de-presion-de-alta-precision-hx711-24bits

[10] Electrónica El Faro. Detector de obstáculos infrarrojos PIR HC-SR501. Disponible en: https://electronicaelfaro.com/detector-de-obstaculos-infrarrojos-pir-hc-sr501

[11] Electrónica El Faro. ESP32 Wemos D1 R32. Disponible en: https://electronicaelfaro.com/esp32-wemos-d1-r32

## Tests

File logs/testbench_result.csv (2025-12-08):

%,RPM,Empuje,Par,Intensidad,Voltaje
0,9973.4,121843,124020,0.55,0.0
10,99502.48,121880,145410,0.63,0.0
20,99502.48,121846,139398,0.69,0.0
30,7368.29,121855,136614,0.73,0.0
Kt,211367.2464025948
Kv,0.0
Potencia Eléctrica (W)
0.0,0.0,0.0,0.0
Potencia Mecánica (W)
129527976.94820562,1515154073.1019857,1452509782.5615199,105412117.11729945
Rendimiento,0.0

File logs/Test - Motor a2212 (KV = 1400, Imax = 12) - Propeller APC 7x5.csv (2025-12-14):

% | RPM | Empuje | Par | Intensidad | Voltaje
0 | 0 | 0.19 | -5.11 | 0.38 | 12.0
10 | 0 | 0.2 | 35.27 | 0.48 | 12.0
20 | 3284.97 | 48.62 | 107.32 | 0.58 | 12.0
30 | 4605.47 | 94.67 | 141.75 | 0.77 | 12.0
40 | 5533.01 | 140.56 | 171.22 | 0.89 | 12.0
50 | 6442.61 | 184.2 | 232.44 | 1.18 | 12.0
60 | 7179.61 | 235.5 | 314.91 | 1.4 | 12.0
70 | 8086.25 | 302.96 | 397.02 | 1.66 | 12.0
80 | 8956.56 | 388.2 | 530.47 | 1.88 | 12.0
90 | 9870.05 | 455.82 | 618.61 | 2.75 | 12.0
100 | 10689.47 | 541.62 | 719.62 | 2.96 | 12.0
Kt | [-0.0013191868421052633, 0.007208306250000001, 0.018151882758620688, 0.01805931818181818, 0.018872676404494387, 0.019324037288135597, 0.022066193571428576, 0.02346244698795181, 0.027680376063829792, 0.02206750581818182, 0.023849568243243247]
Kv | [0.0, 0.0, 28.666771164619064, 40.190307550911626, 48.28462102288572, 56.22237846095593, 62.65391675455504, 70.56584331969573, 78.16073082621166, 86.13243491823316, 93.28322339657912]
Potencia El�ctrica (W)
4.5600000000000005 | 5.76 | 6.959999999999999 | 9.24 | 10.68 | 14.16 | 16.799999999999997 | 19.919999999999998 | 22.56 | 33.0 | 35.519999999999996
Potencia Mec�nica (W)
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

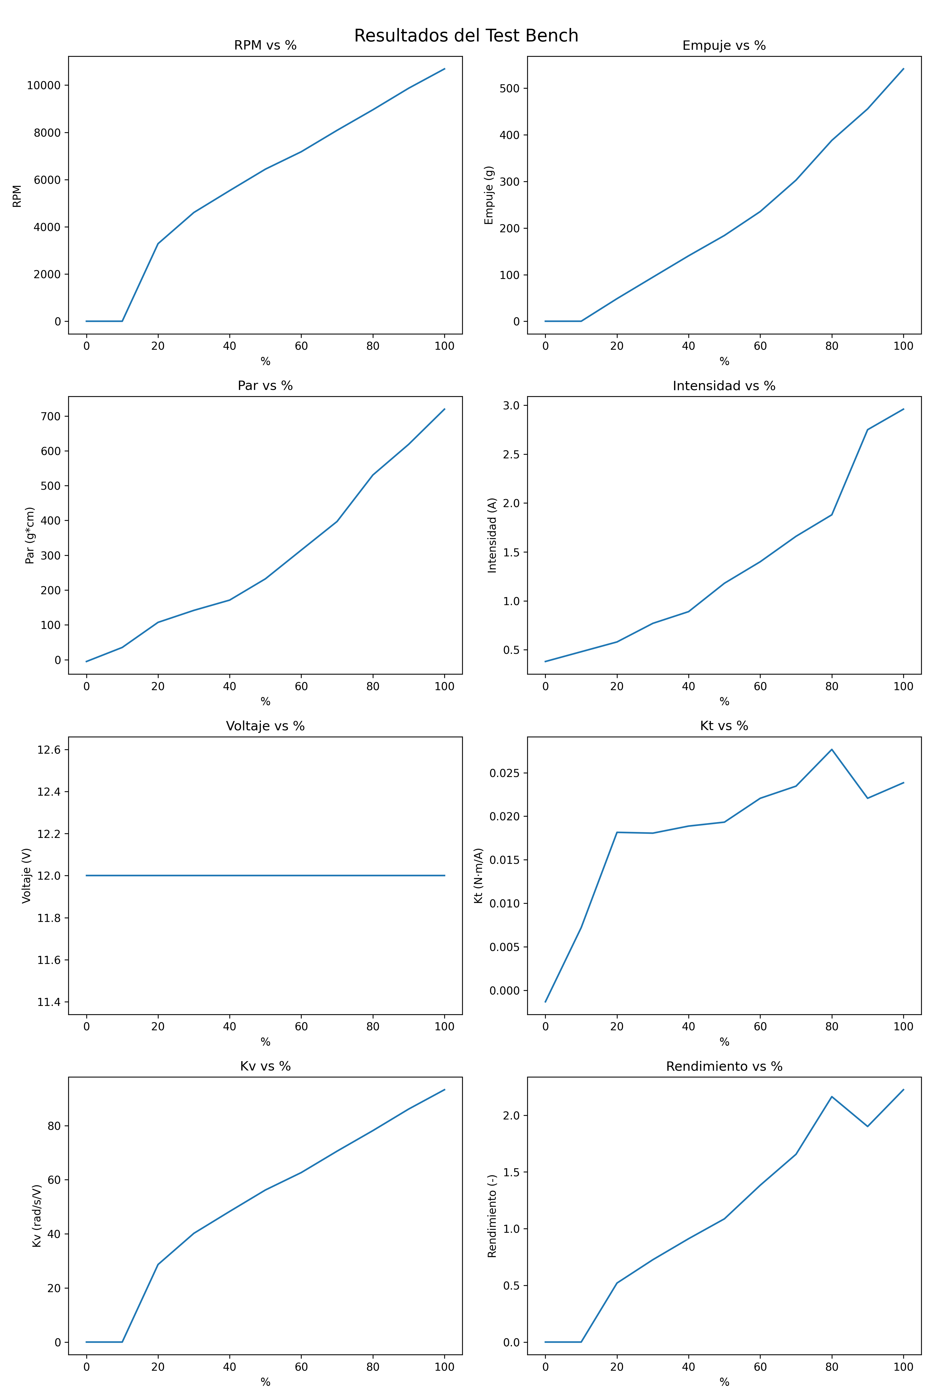
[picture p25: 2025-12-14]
fig/Test - Motor a2212 - Propeller APC 7x5.png

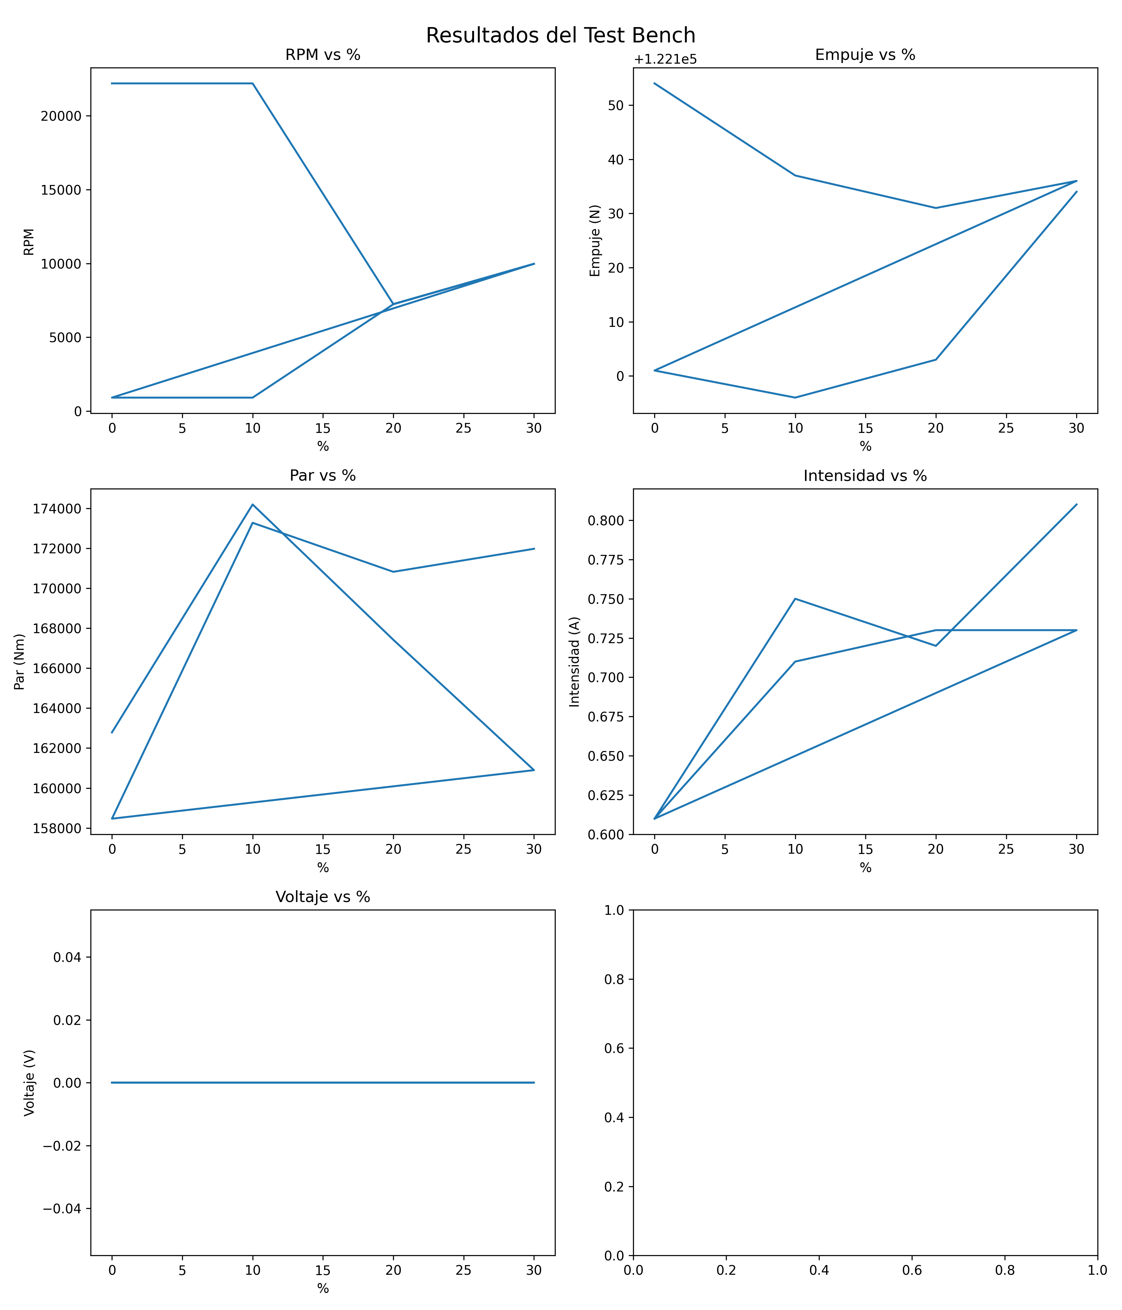
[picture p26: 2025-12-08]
fig/testbench_result.png

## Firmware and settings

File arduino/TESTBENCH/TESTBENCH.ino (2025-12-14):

// NOMBRE: Ruben Sahuquillo Redondo
// ASIGNATURA: Lenguajes de Alto Nivel para Aplicaciones Industriales
// DESCRIPCION: Firmware Banco de Pruebas de Motores


// --- LIBRERIAS --- //
#include <HX711.h>
#include <WiFi.h>
#include <ArduinoJson.h>
#include <PubSubClient.h>

// --- ESTADOS --- //
#define STOP 0
#define TESTING 1
#define TARE 2
#define CALIB 3

// --- PINES --- //
#define SCK2 17
#define DT2 16
#define SCK1 27
#define DT1 14
#define TACOMETRO 25
#define SENSOR_CORRIENTE 34
#define MOTOR_PIN 26
#define WAKE_BUTTON_PIN 12

// --- VARIABLES --- //
const char* ssid = "OPPO A53";
const char* password = "611b10a883c5";
const char* mqtt_server = "10.74.94.63";

int vel_init = 0;
int vel_last = 0;
int step = 0;
float stepTime = 0.0;
int ciclos = 0;
bool measure_rpm = false;
bool measure_thrust = false;
bool measure_torque = false;
bool measure_current = false;

int estado = STOP;
int estadoAnterior = estado;

float palanca = 6;
float peso = 0.0;
float RPM = 0.0;
float empuje = 0.0;
float par = 0.0;
float consumo = 0.0;

unsigned long pulseInterval;
unsigned long lastPulseTime;
unsigned long now;
unsigned long before;

const float voltToAmp = 0.185;
float escala = 1.0;
float max_current = 0.0;

unsigned int porcentaje = 0;
const unsigned int pwmFreq = 50;
const unsigned int pwmResolution = 16;
unsigned int dutyCycle = 0;
const unsigned int minDuty = 3277;
const unsigned int maxDuty = 6554;


// --- OBJETOS --- //
HX711 balanza1;
HX711 balanza2;
WiFiClient espClient;
PubSubClient client(espClient);
StaticJsonDocument<512> doc;


// --- INTERRUPCIONES --- //
void IRAM_ATTR pulseISR() {
  unsigned long now = micros();
  unsigned long diff = now - lastPulseTime;
  //Si la diferencia entre pulsos consecutivos es mayor a 200 uS, actualizar ultimo pulso
  if (diff > 200) {
    pulseInterval = diff;
    lastPulseTime = now;
  }
}


//--- FUNCION LEER VELOCIDAD ---//
float leerVelocidad() {
  unsigned long intervalo;
  //Desactivar interrupciones
  noInterrupts();
  //Asignar tiempo medido entre pulsos a variable
  intervalo = pulseInterval;
  //Reactivar interrupciones
  interrupts();
  //Si el intervalo es nulo, devolver velocidad == 0
  if (intervalo == 0) {
    return 0.0;
  }
  float revPerSec = 1000000.0f / (float)intervalo;      //Convertir lectura a rev/sec
  return revPerSec * 60.0f;                             //Convertir y devolver lectura en RPM
}


//--- FUNCION GIRAR MOTOR ---//
void giraMotor(int pct) {
  unsigned int duty = map(pct, 0, 100, minDuty, maxDuty);   //Mapear procentaje a velocidad en terminos de duty cicle
  ledcWrite(MOTOR_PIN, duty);                               //Enviar comando PWM al pin conectado con el motor
}


//--- FUNCION LEER CONSUMO ---//
float leerConsumo() {
  long lectura = 0;
  //Bucle para acumular lecturas del sensor de corriente
  for (unsigned int i = 0; i < 10; i++) {
    lectura += analogRead(SENSOR_CORRIENTE);
  }
  lectura /= 10;                                    //Calcular la media de las lecturas
  float volt = (float)lectura * 3.3f / 4095.0f;     //Convertir a valor en voltios (lecturas ADC a voltaje)
  float amp = (volt - 1.435) / voltToAmp;           //Convertir voltios en amperios
  return amp;                                       //devolver corriente estimada
}


//--- FUNCION LEER BALANZA ---//
float leerBalanza(HX711 &balanza) {
  return balanza.get_units(5);            //Promedia 5 lecturas
}


// --- FUNCION CONFIGURAR WIFI --- //
void configWifi() {
  WiFi.mode(WIFI_STA);                        //Configurar modulo Wifi del uC en modo estación
  WiFi.begin(ssid, password);                 //Conectarse con red Wifi indicada
  Serial.print("Conectando a WiFi");
  //Bucle de espera para conectarse a la red Wifi
  while (WiFi.status() != WL_CONNECTED) {
    delay(300);
    Serial.print(".");
  }
  Serial.println("WiFi conectado");
  Serial.print("IP: ");
  Serial.println(WiFi.localIP());         //Mostrar ip
}


// --- FUNCION CONFIGURAR MQTT --- //
void configMQTT() {
  client.setBufferSize(2048);           //Configurar tamaño del buffer para recepcion de datos
  client.setServer(mqtt_server, 1883);  //Conectarse a servidor MQTT indicado
  client.setCallback(mqttCallback);     //Añadir funcion de callback asociada a la recepcion de mensajes
}


// --- FUNCION RECONECTAR MQTT --- //
void MQTTreconnect() {
  //Mientras el cliente MQTT no esté conectado, intentar reconectarse y suscribirse al topico de recepcion de datos
  while (!client.connected()) {
    Serial.print("Intentando conexión MQTT...");
    if (client.connect("ESP32")) {
      Serial.println("Conectado al broker MQTT");
      client.subscribe("esp32/input");
    }
  }
}


// --- FUNCION CALLBACK MQTT --- //
void mqttCallback(char* topic, byte* payload, unsigned int length) {
  Serial.println("\n--- MQTT MESSAGE RECEIVED ---");
  Serial.println("LENGTH: " + String(length));
  String jsonStr;                                     //Crear string para almacenar cadena 
  jsonStr.reserve(length + 1);                        //Reservar espacio para string equivalente a la longitud de los datos recibidos + 1
  //Bucle para recorrer caracteres recibidos y añadirlos al string
  for (unsigned int i = 0; i < length; i++) {
    jsonStr += (char)payload[i];
  }
  Serial.print("Topic: ");
  Serial.println(topic);
  Serial.print("Payload: ");
  Serial.println(jsonStr);

  StaticJsonDocument<8192> doc;                                 //Objeto instanciado para trabajar con cadenas en formato JSON
  DeserializationError error = deserializeJson(doc, jsonStr);   //Desserializar cadena y añade error a la variable error si sucede un error
  
  //Si existe algun error, mostrarlo por consola
  if (error) {
    Serial.print("ERROR leyendo JSON: ");
    Serial.println(error.c_str());
    return;
  }

  // Leer acción
  String action = doc["action"] | "";
  Serial.print("Acción recibida: ");
  Serial.println(action);

  //Si la accion es start
  if (action == "start") {
    Serial.println("\n--- CONFIGURACIÓN RECIBIDA ---");
    //Preparar JSON para buscar datos de forma simple
    serializeJsonPretty(doc["data"], Serial);
    //Extraccion de datos y asignacion a variables correspondientes
    vel_init  = doc["data"]["vel_init"].as<int>();
    vel_last  = doc["data"]["vel_last"].as<int>();
    step      = doc["data"]["step"].as<int>();
    stepTime  = doc["data"]["stepTime"].as<float>();
    ciclos    = doc["data"]["cicles"].as<int>();
    measure_rpm     = doc["data"]["measure_rpm"].as<bool>();
    measure_thrust  = doc["data"]["measure_thrust"].as<bool>();
    measure_torque  = doc["data"]["measure_torque"].as<bool>();
    measure_current = doc["data"]["measure_current"].as<bool>();
    max_current = doc["data"]["max_current"].as<float>();

    Serial.println("\n--- VALORES ACTUALIZADOS ---");
    Serial.print("vel_init: "); Serial.println(vel_init);
    Serial.print("vel_last: "); Serial.println(vel_last);
    Serial.print("step: "); Serial.println(step);
    Serial.print("stepTime: "); Serial.println(stepTime);
    Serial.print("cicles: "); Serial.println(ciclos);
    Serial.print("measure_rpm: "); Serial.println(measure_rpm);
    Serial.print("measure_thrust: "); Serial.println(measure_thrust);
    Serial.print("measure_torque: "); Serial.println(measure_torque);
    Serial.print("measure_current: "); Serial.println(measure_current);
    Serial.print("max_current: "); Serial.println(max_current);
    Serial.println("\nVariables internas actualizadas.");

    estado = TESTING;         //Actualizar estado a TESTING
    before = millis();    
    porcentaje = vel_init;    //Asignar velocidad inicial(%)
  }
  //Si la accion es stop, cambiar estado a STOP
  else if (action == "stop") {
    estado = STOP;
  }
  //Si la accion es tare, y el estado actual no es TESTING, cambiar a estado TARE
  else if (action == "tare"){
    if (estado != TESTING){
      estado = TARE;
    }
  }
  //Si la accion es calib, y el estado actual no es TESTING, cambiar a estado CALIB
  else if (action == "calibrate"){
    peso  = doc["data"]["weight"].as<float>();
    if (estado != TESTING){
      estado = CALIB;
    }
  }
  //Si la accion no es ninguna de la anterior, mostrar mensaje
  else {
    Serial.println("Comando no reconocido.");
  }

  Serial.println("--- END MQTT MESSAGE ---\n");
}


// --- FUNCION PUBLICAR MQTT JSON --- //
void JSONpublisher(int porcentaje, float RPM, float consumo, float empuje, float par) {
  doc.clear();                                //Limpiar objeto doc
  doc["%"] = porcentaje;                      //Añadir porcentaje
  doc["RPM"] = RPM;                           //Añadir velocidad medida
  doc["Intensidad"] = consumo;                //Añadir corriente medida
  doc["Empuje"] = empuje;                     //Añadir empuje medido
  doc["Par"] = par;                           //Añadir par medido
  char buffer[256];                           //Buffer para almacenar datos
  size_t n = serializeJson(doc, buffer);      //Serializar datos
  client.publish("esp32/output", buffer, n);  //Publicar datos por MQTT
}


// --- FUNCION CONFIGURAR HX711 --- //
void configHX711() {
  Serial.println("Configurando Celdas de Carga");
  balanza1.begin(DT1, SCK1);        //Iniciar celda de carga 1
  while (!balanza1.is_ready());     
  Serial.println("Celda 1 lista");
  balanza2.begin(DT2, SCK2);        //Iniciar celda de carga 2
  while (!balanza2.is_ready());
  Serial.println("Celda 2 lista");
}


// --- FUNCION INICIAR TEST --- //
void testInit() {
  now = millis();
  //Comprobar tiempo entre pasos
  if ((now - before) >= (stepTime * 1000.0)) {
    before = now;
    //Si se llego a la velocidad final
    if (porcentaje > vel_last) {
      porcentaje = vel_init;    // Reiniciar porcentaje
      giraMotor(porcentaje);    // Detener motor
      delay(1000);
      ciclos--;                 // Restar 1 al contador de ciclos restantes
      Serial.println("TEST FINALIZADO");
      // Si se acabaron los ciclos se pasa a estado de STOP
      if (ciclos == 0){
        estado = STOP;
      }
      return;
    }
    //Si la velocidad (%) no es la final
    if (porcentaje < vel_last + step) {
      Serial.println(porcentaje);
      giraMotor(porcentaje);      // Se gira el motor a la velocidad indicada (%)
      //Si se quiere medir velocidad
      if (measure_rpm){
        RPM = leerVelocidad();
        Serial.print("Velocidad: ");
        Serial.println(RPM);
      }
      //Si se quiere medir empuje
      if (measure_thrust){
        empuje = -leerBalanza(balanza1);
        Serial.print("Empuje: ");
        Serial.println(empuje);
      }
      //Si se quiere medir par
      if (measure_torque){
        par = -leerBalanza(balanza2) * palanca;
        Serial.print("Par: ");
        Serial.println(par);
      }
      //Si se quiere medir corriente
      if (measure_current){
        consumo = leerConsumo();
        //Si el consumo es mayor o igual a la corriente maxima admisible
        if (consumo >= max_current) {
          testStop();         //Detener test
          estado = STOP;      //Cambiar a estado de STOP
          //Publicar mensaje informativo por MQTT
          client.publish("esp32/output","Corriente superior a la máxima");
        }
      }
      // Publicar datos en formato JSON
      JSONpublisher(porcentaje, RPM, consumo, empuje, par);
      Serial.println("DATOS PUBLICADOS");
      //Incrementar velocidad (%)
      porcentaje += step;
    }
  }
}


// --- FUNCION DETENER TEST --- //
void testStop(){
  giraMotor(0);           //Detener giro del motor
  delay(2000);
  //Reseteo de variables
  RPM = 0.0;
  empuje = 0.0;
  par = 0.0;
  consumo = 0.0;
  pulseInterval = 0.0;
}


// --- SETUP --- //
void setup() {
  //Inicio comunicacion serial
  Serial.begin(115200);
  while (!Serial){;}
  //Configuracion conexion wifi
  configWifi();
  //Configuracion comunicacion MQTT
  configMQTT();
  //Configuracion de pines
  pinMode(TACOMETRO, INPUT_PULLUP);
  pinMode(SENSOR_CORRIENTE, INPUT);
  //Declaracion de interrupcion
  attachInterrupt(digitalPinToInterrupt(TACOMETRO), pulseISR, FALLING);
  //Configurar celdas de carga
  configHX711();
  //Configurar motor y PWM
  ledcAttach(MOTOR_PIN, pwmFreq, pwmResolution);
  ledcWrite(MOTOR_PIN, map(0, 0, 100, minDuty, maxDuty));
  delay(5000);
  //Comenzar ensayo motor detenido
  testStop();
}


// --- LOOP --- //
void loop() {
  //Si no hay cliente MQTT conectado, intentar reconectar
  if (!client.connected()) {
    MQTTreconnect();
  }
  //Mantener cliente MQTT activo
  client.loop();

  //Maquina de estados
  switch (estado) {
    //Estado de STOP
    case STOP:
      testStop();
      if (estadoAnterior != STOP){
        Serial.println("STOPPED");
      }
      break;

    //Estado de TESTING
    case TESTING:
      if (estadoAnterior != TESTING){
        Serial.println("TESTING");
      }
      testInit();
      break;

    //Estado de TARE
    case TARE:
      balanza1.tare(20);          //Tarar celda de carga 1
      Serial.println("TARA 1");
      balanza2.tare(20);          //Tarar celda de carga 2
      Serial.println("TARA 2");
      estado = STOP;              //Cambiar estado a STOP
      client.publish("esp32/output","Tara Realizada");
      break;

    //Estado de CALIB
    case CALIB:
      balanza1.set_scale();       //Escalar celda de carga con escala = 1
      delay(1000);
      Serial.println(peso);
      escala = balanza1.get_value(10) / peso;   //Calcular escalar celda de carga 1
      balanza1.set_scale(escala);               //Escalar celda de carga 1  
      balanza2.set_scale(escala);               //Escalar celda de carga 2
      Serial.println("CALIBRADA 1 y 2");
      estado = STOP;                            //Cambiar estado STOP
      client.publish("esp32/output","Calibración Realizada");
      break;
  }
  estadoAnterior = estado;       //Actualizar estado anterior
}
